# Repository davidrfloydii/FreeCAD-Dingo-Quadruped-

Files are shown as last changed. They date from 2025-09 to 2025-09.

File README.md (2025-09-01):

# FreeCAD-Dingo-Quadruped-
A repository containing the FreeCAD CAD files for the robot, firmware for microcontrollers, and code for the robot

This is a version of the original design located [here](https://github.com/Yerbert/DingoQuadruped) and is intended to recreate the core functionality utilzing all open source tools.

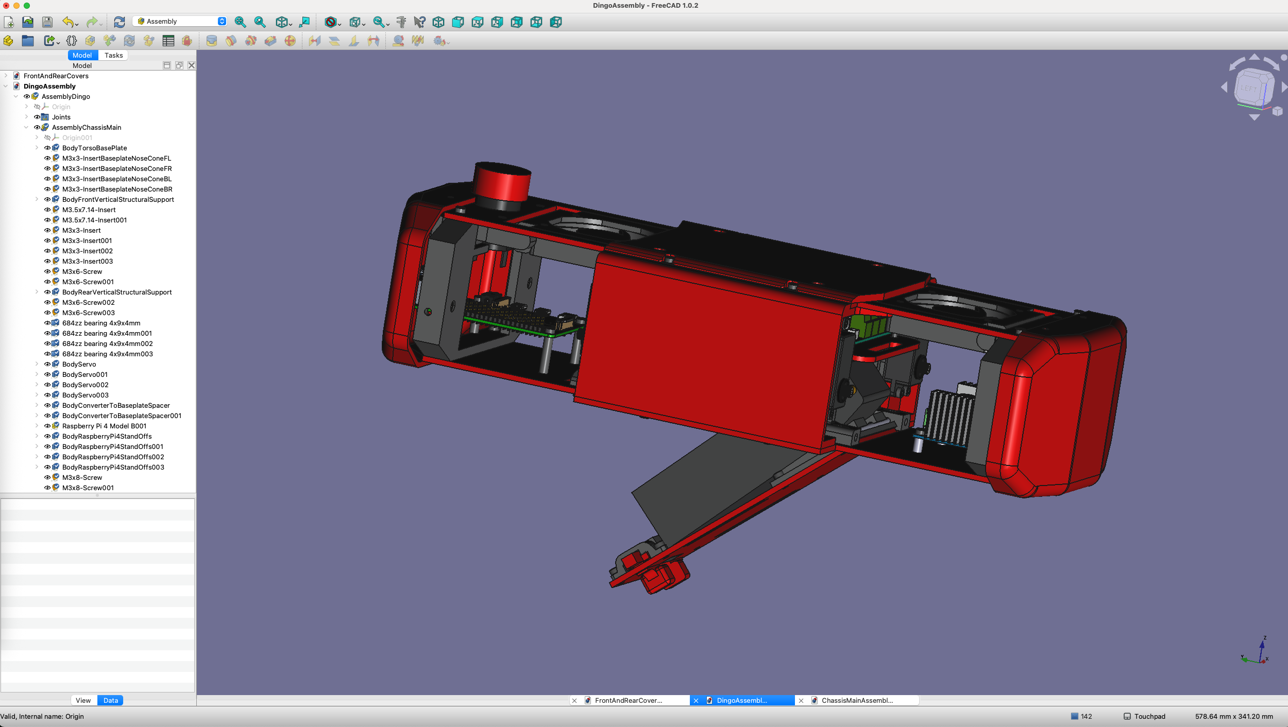
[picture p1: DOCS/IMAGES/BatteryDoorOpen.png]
Current Assembly State


# Directory Structure
The following describes the diretory structure. Note: The FreeCAD 1.0 Assembly workbench is used for putting all parts and sub-assemblies together into a single document.

-  BOM - Will hold a generated bill of materials once the assembly is completed.
-  DingoAssembly.FCStd the parent assembly to open containing the fully assembled robot.
-  EDA - Will contain KiCAD files for PCBs
-  LegParts - Contains all the CAD files that make up the legs of the robot.
-  OffTheShelfComponents - Contains standar parts that are ordered but used to positiong items in the custom parts. Some are step file format and others were modeled using FreeCAD.
-  Stand - Will contain the stand used for testing the robot.
-  SubAssemblies - Contains various SubAssemblies that are part of the parent assembly.
  -  BatteryTray - The SubAssembly for the battery holder and related parts.
  -  BL_Leg - The SubAssembly for the back left leg.
  -  BR_Leg - The SubAssembly for the back right leg.
  -  Chassis_Main - The SubAssembly that contains all of the parts of the main chassis of the robot.
  -  Fasteners - Contains standard screws, nuts, bolts, and heat inserts used from the fasteners workbench.
  -  FL_Leg - The SubAssembly for the front left leg.
  -  FR_Leg - The SubAssembly for the front right leg.
  -  Middle_Platform - The SubAssembly that sits in the center of the robot and houses various electronics components.

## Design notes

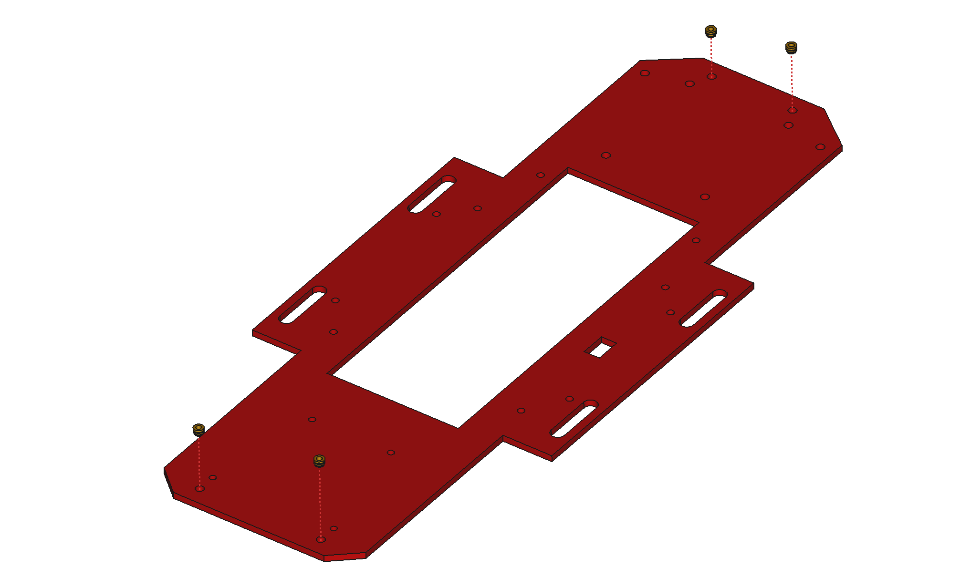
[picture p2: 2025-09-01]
SubAssemblies/Chassis_Main/Docs/Images/BaseplateHeatInserts.png

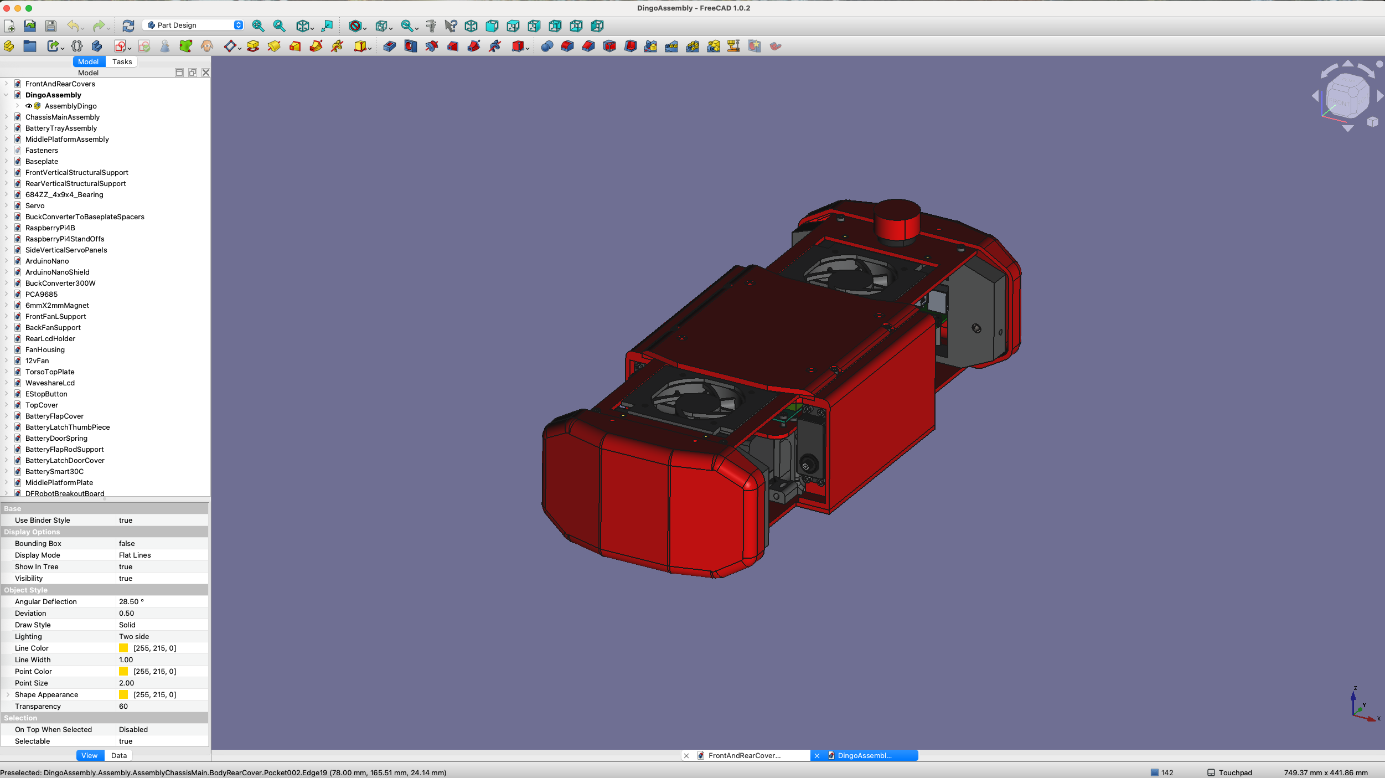
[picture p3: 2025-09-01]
DOCS/IMAGES/DingoFreeCADProject.png

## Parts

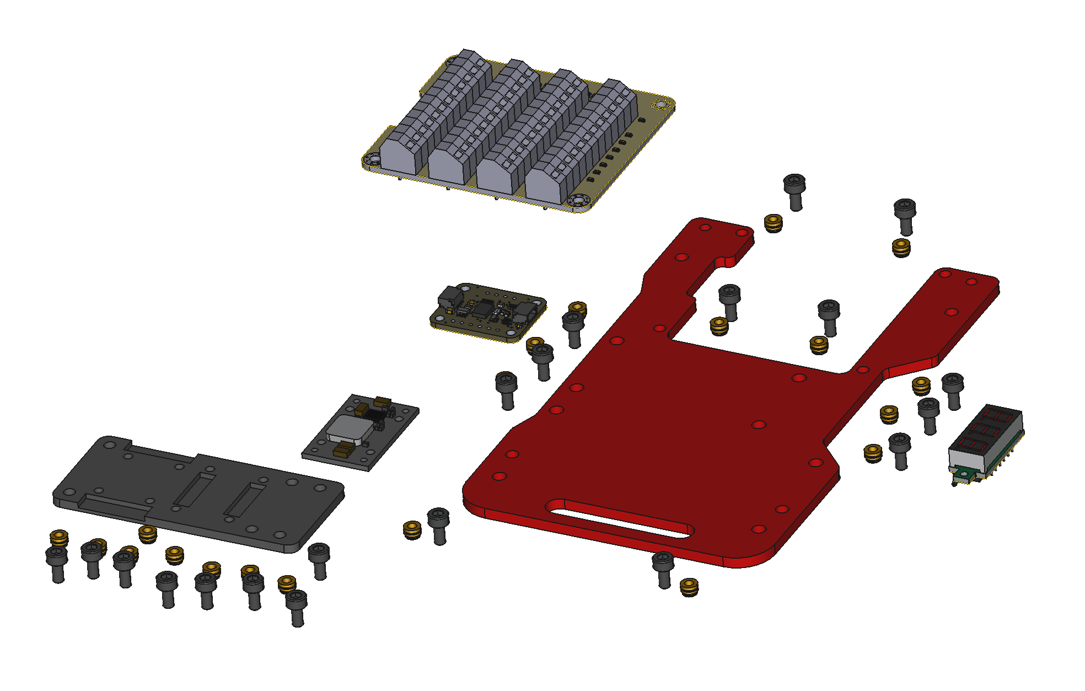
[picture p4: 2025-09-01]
SubAssemblies/Middle_Platform/Docs/Images/Middle SubAssembly Parts Laid Out.png

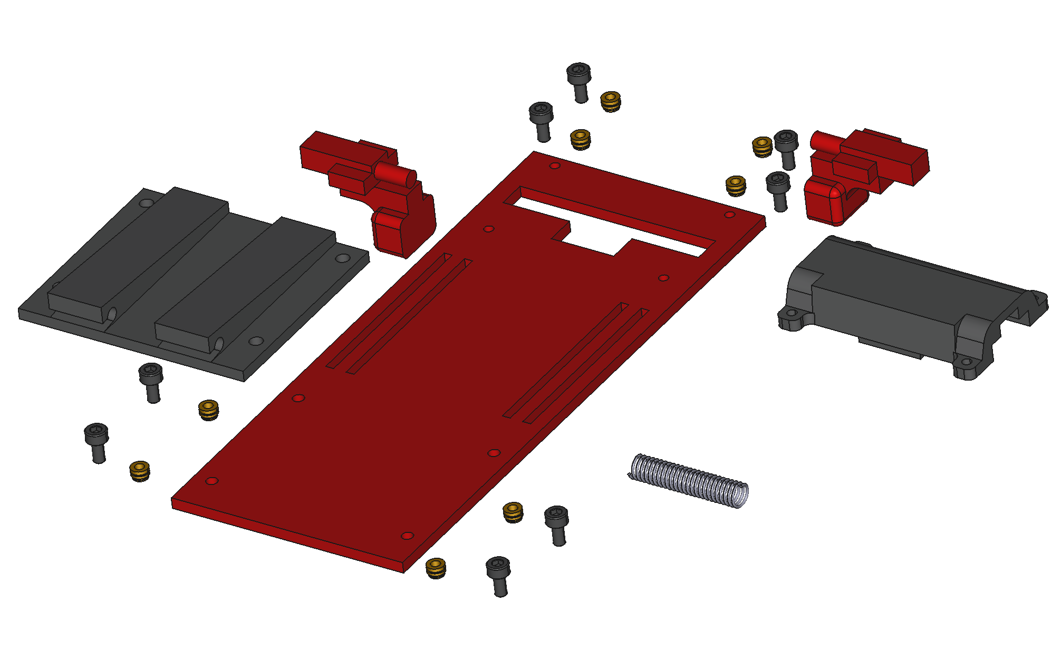
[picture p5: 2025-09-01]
SubAssemblies/BatteryTray/Docs/Images/Battery Tray SubAssembly Parts Overview.png

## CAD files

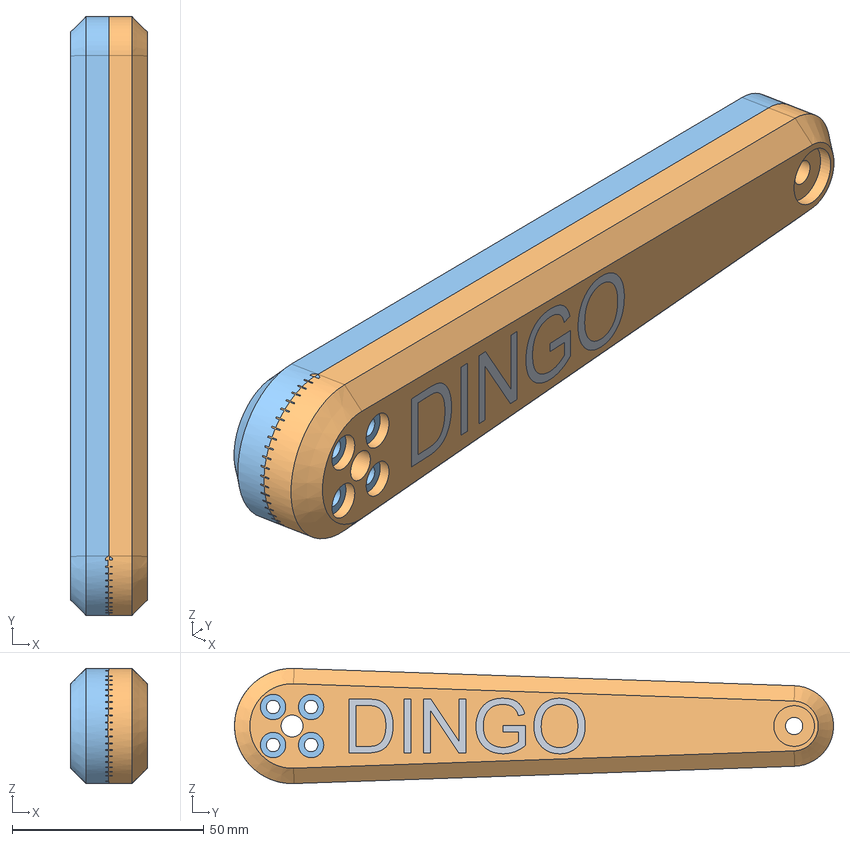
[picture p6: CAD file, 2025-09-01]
LegParts/LegUpper.FCStd
20.0 x 156.0 x 30.0 mm
BodyLegUpperCommon
BodyLegUpperRight
BodyLegUpperLeft

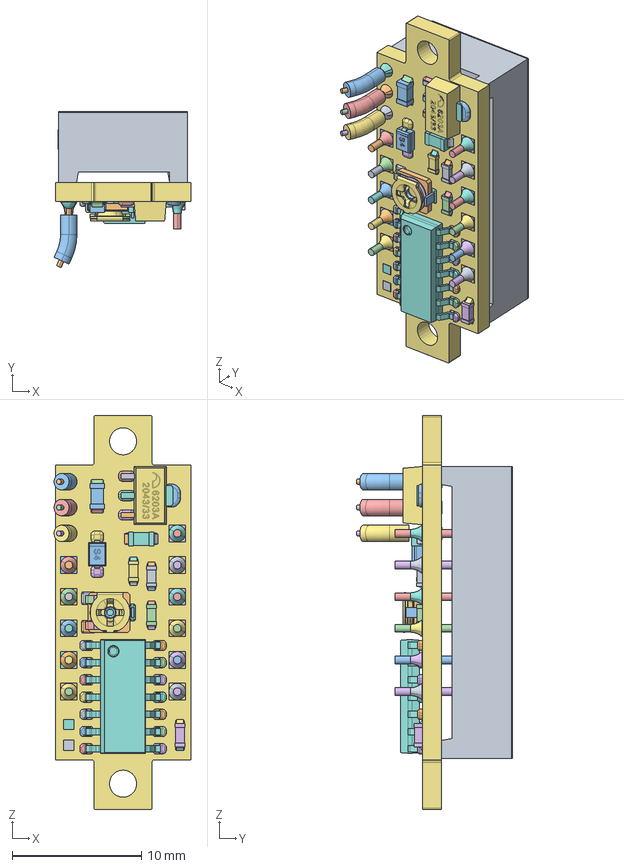
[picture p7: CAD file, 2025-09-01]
OffTheShelfComponents/BatteryLcdDisplay.FCStd
10.6 x 12.1 x 30.5 mm
Voltmeter_2,8_Display-3-Digi_DC 0V-100V_Red.stp
Voltmeter_2,8_Display-3-Digi_DC 0V-100V_Red.stp001
Voltmeter_2,8_Display-3-Digi_DC 0V-100V_Red.stp002
Voltmeter_2,8_Display-3-Digi_DC 0V-100V_Red.stp003
Voltmeter_2,8_Display-3-Digi_DC 0V-100V_Red.stp004
Voltmeter_2,8_Display-3-Digi_DC 0V-100V_Red.stp005
Voltmeter_2,8_Display-3-Digi_DC 0V-100V_Red.stp006
Voltmeter_2,8_Display-3-Digi_DC 0V-100V_Red.stp007
Voltmeter_2,8_Display-3-Digi_DC 0V-100V_Red.stp008
Voltmeter_2,8_Display-3-Digi_DC 0V-100V_Red.stp009
Voltmeter_2,8_Display-3-Digi_DC 0V-100V_Red.stp010
Voltmeter_2,8_Display-3-Digi_DC 0V-100V_Red.stp011
Voltmeter_2,8_Display-3-Digi_DC 0V-100V_Red.stp012
Voltmeter_2,8_Display-3-Digi_DC 0V-100V_Red.stp013
Voltmeter_2,8_Display-3-Digi_DC 0V-100V_Red.stp014
Voltmeter_2,8_Display-3-Digi_DC 0V-100V_Red.stp015
Voltmeter_2,8_Display-3-Digi_DC 0V-100V_Red.stp016
Voltmeter_2,8_Display-3-Digi_DC 0V-100V_Red.stp017
Voltmeter_2,8_Display-3-Digi_DC 0V-100V_Red.stp018
Voltmeter_2,8_Display-3-Digi_DC 0V-100V_Red.stp019
Voltmeter_2,8_Display-3-Digi_DC 0V-100V_Red.stp020
Voltmeter_2,8_Display-3-Digi_DC 0V-100V_Red.stp021
Voltmeter_2,8_Display-3-Digi_DC 0V-100V_Red.stp022
Voltmeter_2,8_Display-3-Digi_DC 0V-100V_Red.stp023
Voltmeter_2,8_Display-3-Digi_DC 0V-100V_Red.stp024
Voltmeter_2,8_Display-3-Digi_DC 0V-100V_Red.stp025
Voltmeter_2,8_Display-3-Digi_DC 0V-100V_Red.stp026
Voltmeter_2,8_Display-3-Digi_DC 0V-100V_Red.stp027
Voltmeter_2,8_Display-3-Digi_DC 0V-100V_Red.stp028
Voltmeter_2,8_Display-3-Digi_DC 0V-100V_Red.stp029
Voltmeter_2,8_Display-3-Digi_DC 0V-100V_Red.stp030
Voltmeter_2,8_Display-3-Digi_DC 0V-100V_Red.stp031
Voltmeter_2,8_Display-3-Digi_DC 0V-100V_Red.stp032
Voltmeter_2,8_Display-3-Digi_DC 0V-100V_Red.stp033
Voltmeter_2,8_Display-3-Digi_DC 0V-100V_Red.stp034
Voltmeter_2,8_Display-3-Digi_DC 0V-100V_Red.stp035
Voltmeter_2,8_Display-3-Digi_DC 0V-100V_Red.stp036
Voltmeter_2,8_Display-3-Digi_DC 0V-100V_Red.stp037
Voltmeter_2,8_Display-3-Digi_DC 0V-100V_Red.stp038
Voltmeter_2,8_Display-3-Digi_DC 0V-100V_Red.stp039
Voltmeter_2,8_Display-3-Digi_DC 0V-100V_Red.stp040
Voltmeter_2,8_Display-3-Digi_DC 0V-100V_Red.stp041
Voltmeter_2,8_Display-3-Digi_DC 0V-100V_Red.stp042
Voltmeter_2,8_Display-3-Digi_DC 0V-100V_Red.stp043
Voltmeter_2,8_Display-3-Digi_DC 0V-100V_Red.stp044
Voltmeter_2,8_Display-3-Digi_DC 0V-100V_Red.stp045
Voltmeter_2,8_Display-3-Digi_DC 0V-100V_Red.stp046
Voltmeter_2,8_Display-3-Digi_DC 0V-100V_Red.stp047
Voltmeter_2,8_Display-3-Digi_DC 0V-100V_Red.stp048
Voltmeter_2,8_Display-3-Digi_DC 0V-100V_Red.stp049
Voltmeter_2,8_Display-3-Digi_DC 0V-100V_Red.stp050
Voltmeter_2,8_Display-3-Digi_DC 0V-100V_Red.stp051
Voltmeter_2,8_Display-3-Digi_DC 0V-100V_Red.stp052
Voltmeter_2,8_Display-3-Digi_DC 0V-100V_Red.stp053
Voltmeter_2,8_Display-3-Digi_DC 0V-100V_Red.stp054
Voltmeter_2,8_Display-3-Digi_DC 0V-100V_Red.stp055
Voltmeter_2,8_Display-3-Digi_DC 0V-100V_Red.stp056
Voltmeter_2,8_Display-3-Digi_DC 0V-100V_Red.stp057
Voltmeter_2,8_Display-3-Digi_DC 0V-100V_Red.stp058
Voltmeter_2,8_Display-3-Digi_DC 0V-100V_Red.stp059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

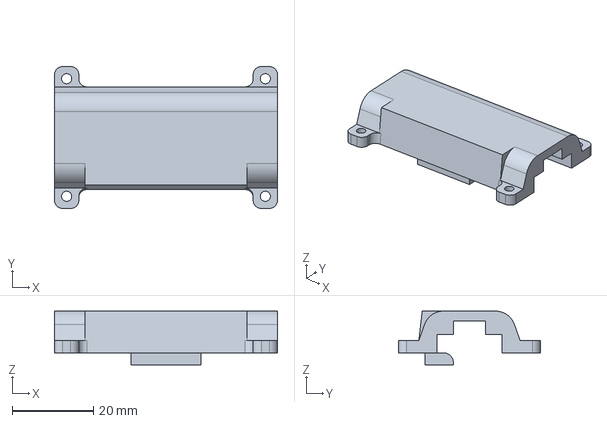
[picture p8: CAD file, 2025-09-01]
SubAssemblies/BatteryTray/Parts/BatteryLatchDoorCover.FCStd
55.0 x 35.0 x 13.3 mm

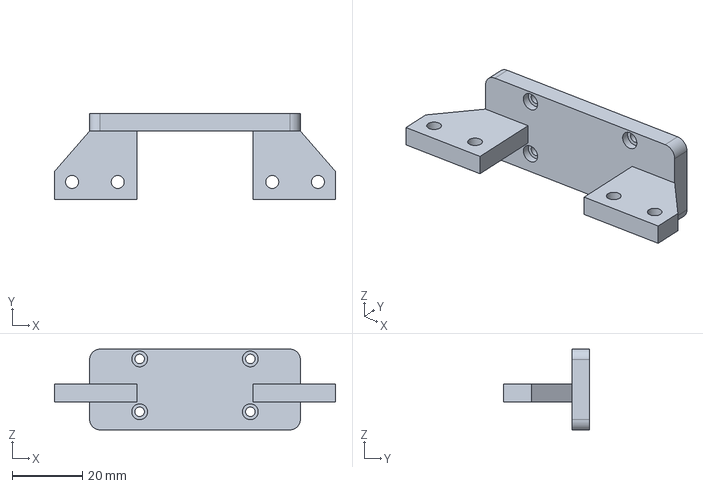
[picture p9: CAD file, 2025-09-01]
SubAssemblies/Chassis_Main/Parts/RearLcdHolder.FCStd
80.0 x 24.5 x 23.0 mm

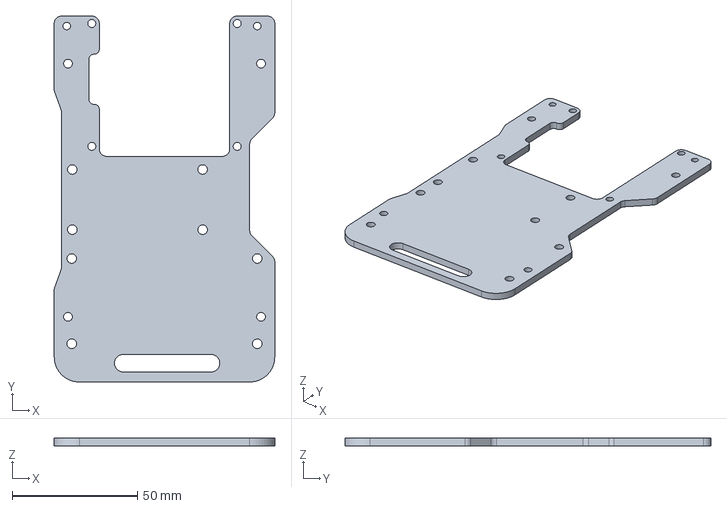
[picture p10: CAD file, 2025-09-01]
SubAssemblies/Middle_Platform/Parts/MiddlePlatformPlate.FCStd
88.0 x 146.0 x 3.00 mm

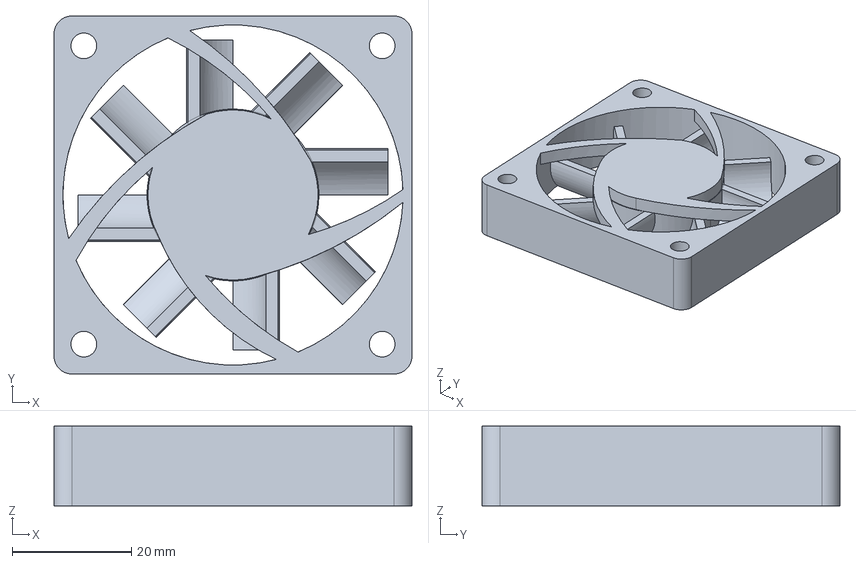
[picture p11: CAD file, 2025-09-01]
OffTheShelfComponents/12vFan.FCStd
60.0 x 60.0 x 13.4 mm

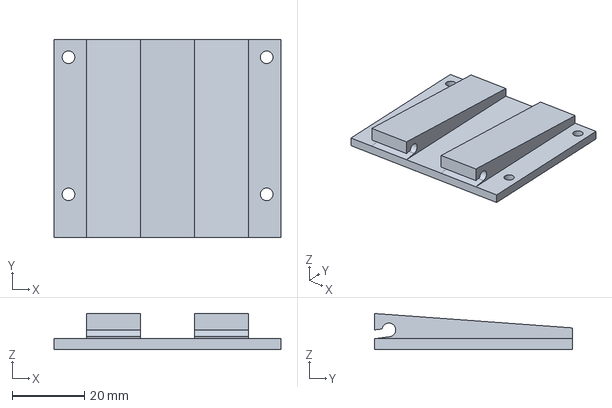
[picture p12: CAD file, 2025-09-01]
SubAssemblies/BatteryTray/Parts/BatteryFlapRodSupport.FCStd
63.0 x 55.0 x 10.0 mm

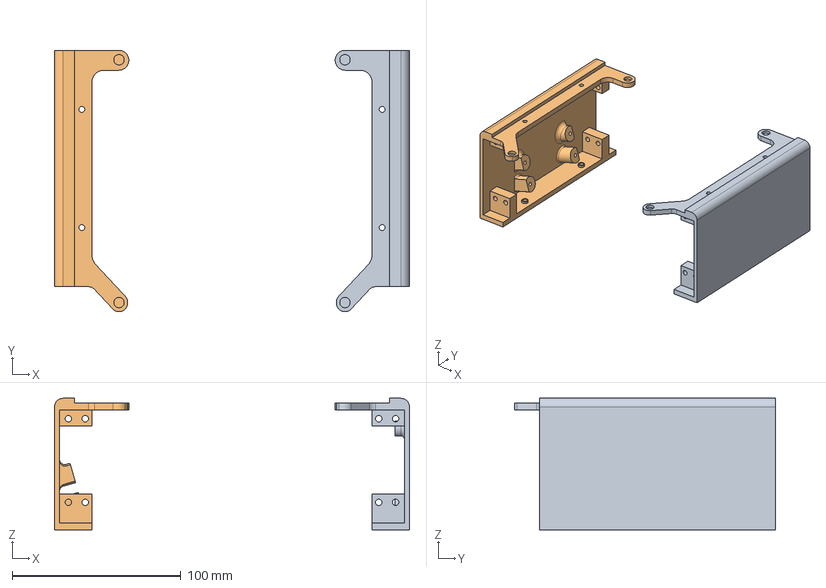
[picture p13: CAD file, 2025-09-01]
SubAssemblies/Chassis_Main/Parts/SideVerticalServoPanels.FCStd
210.2 x 154.8 x 77.9 mm
BodyRightSideVerticalServoPanel
BodyLeftSideVerticalServoPanel

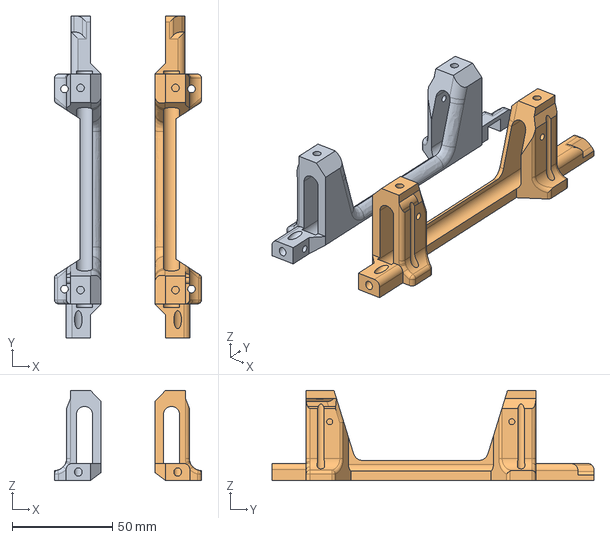
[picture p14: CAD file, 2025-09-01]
SubAssemblies/Middle_Platform/Parts/LeftInnerVerticalSupport.FCStd
73.4 x 160.8 x 45.0 mm
BodyLeftInnerVerticalSupport
BodyRightInnerVerticalSupport

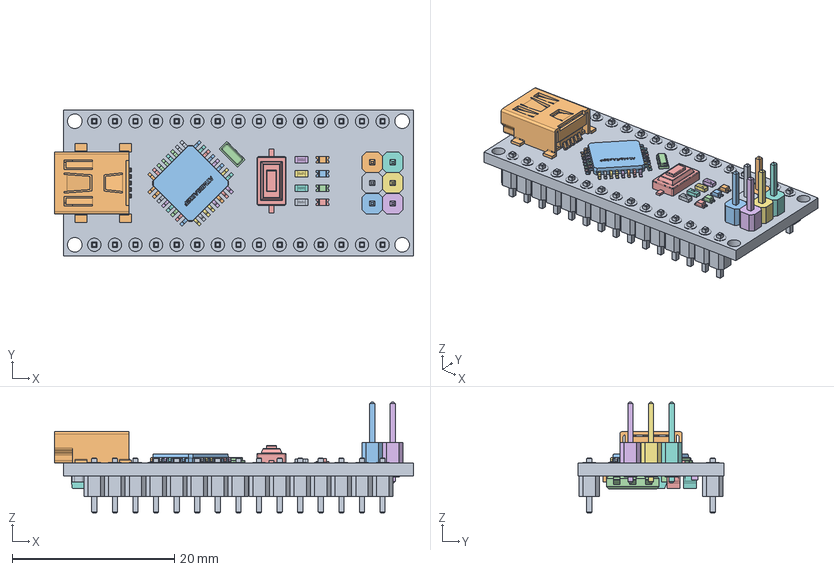
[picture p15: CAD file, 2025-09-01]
OffTheShelfComponents/ArduinoNano.FCStd
44.3 x 18.0 x 13.7 mm
Arduino Nano
Mini USB
ATMEGA328P-AU--3DModel-STEP-56544.step.STEP.STEP.STEP
ATMEGA328P-AU--3DModel-STEP-56544.step.STEP.STEP.STEP001
ATMEGA328P-AU--3DModel-STEP-56544.step.STEP.STEP.STEP002
ATMEGA328P-AU--3DModel-STEP-56544.step.STEP.STEP.STEP003
ATMEGA328P-AU--3DModel-STEP-56544.step.STEP.STEP.STEP004
ATMEGA328P-AU--3DModel-STEP-56544.step.STEP.STEP.STEP005
ATMEGA328P-AU--3DModel-STEP-56544.step.STEP.STEP.STEP006
ATMEGA328P-AU--3DModel-STEP-56544.step.STEP.STEP.STEP007
ATMEGA328P-AU--3DModel-STEP-56544.step.STEP.STEP.STEP008
ATMEGA328P-AU--3DModel-STEP-56544.step.STEP.STEP.STEP009
ATMEGA328P-AU--3DModel-STEP-56544.step.STEP.STEP.STEP010
ATMEGA328P-AU--3DModel-STEP-56544.step.STEP.STEP.STEP011
ATMEGA328P-AU--3DModel-STEP-56544.step.STEP.STEP.STEP012
ATMEGA328P-AU--3DModel-STEP-56544.step.STEP.STEP.STEP013
ATMEGA328P-AU--3DModel-STEP-56544.step.STEP.STEP.STEP014
ATMEGA328P-AU--3DModel-STEP-56544.step.STEP.STEP.STEP015
ATMEGA328P-AU--3DModel-STEP-56544.step.STEP.STEP.STEP016
ATMEGA328P-AU--3DModel-STEP-56544.step.STEP.STEP.STEP017
ATMEGA328P-AU--3DModel-STEP-56544.step.STEP.STEP.STEP018
ATMEGA328P-AU--3DModel-STEP-56544.step.STEP.STEP.STEP019
ATMEGA328P-AU--3DModel-STEP-56544.step.STEP.STEP.STEP020
ATMEGA328P-AU--3DModel-STEP-56544.step.STEP.STEP.STEP021
ATMEGA328P-AU--3DModel-STEP-56544.step.STEP.STEP.STEP022
ATMEGA328P-AU--3DModel-STEP-56544.step.STEP.STEP.STEP023
ATMEGA328P-AU--3DModel-STEP-56544.step.STEP.STEP.STEP024
ATMEGA328P-AU--3DModel-STEP-56544.step.STEP.STEP.STEP025
ATMEGA328P-AU--3DModel-STEP-56544.step.STEP.STEP.STEP026
ATMEGA328P-AU--3DModel-STEP-56544.step.STEP.STEP.STEP027
ATMEGA328P-AU--3DModel-STEP-56544.step.STEP.STEP.STEP028
ATMEGA328P-AU--3DModel-STEP-56544.step.STEP.STEP.STEP029
ATMEGA328P-AU--3DModel-STEP-56544.step.STEP.STEP.STEP030
ATMEGA328P-AU--3DModel-STEP-56544.step.STEP.STEP.STEP031
ATMEGA328P-AU--3DModel-STEP-56544.step.STEP.STEP.STEP032
CSTCE Crystal
2Pin Tactile Switch 6x3.6
0603 Resistor
0603 Resistor001
0603 Resistor002
0603 Resistor003
Blue LED
Green LED
Red LED
Blue LED001
Header 2x3
Header 2x004
Header 2x005
Header 2x006
Header 2x007
Header 2x008
SOT89
1206 Tantalum
0603 Resistor004
0603 Capacitor
1206 Tantalum001
0603 Capacitor001
0603 Capacitor002
0603 Capacitor003
0603 Capacitor004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

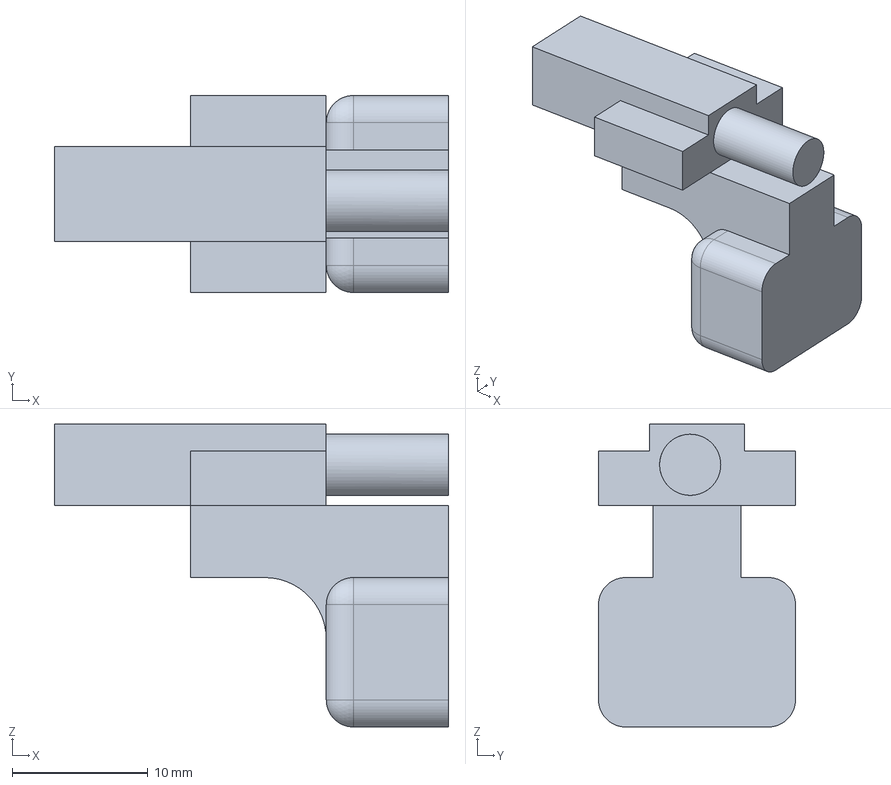
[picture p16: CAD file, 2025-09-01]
SubAssemblies/BatteryTray/Parts/BatteryLatchThumbPiece.FCStd
29.0 x 14.5 x 22.3 mm

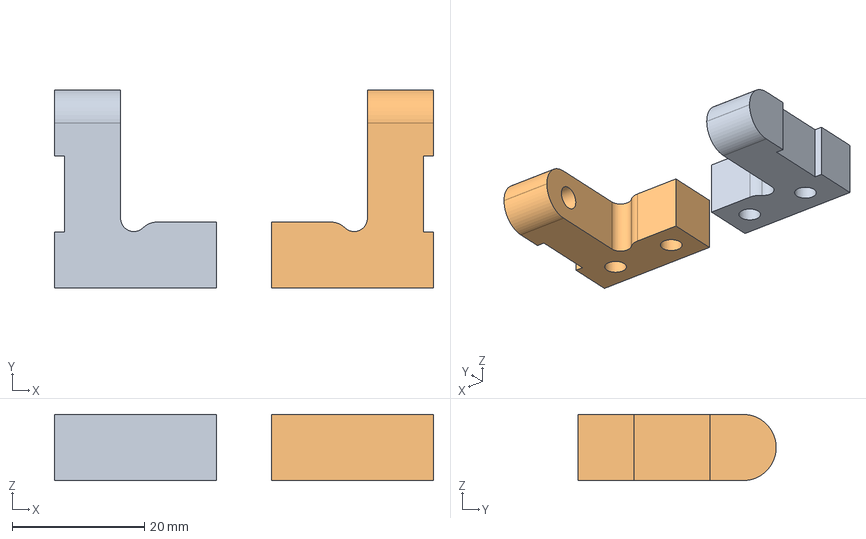
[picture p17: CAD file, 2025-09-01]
SubAssemblies/Chassis_Main/Parts/FrontFanLSupport.FCStd
57.3 x 30.0 x 10.0 mm
BodyFrontFanSupportLeft
BodyFrontFanSupportRight

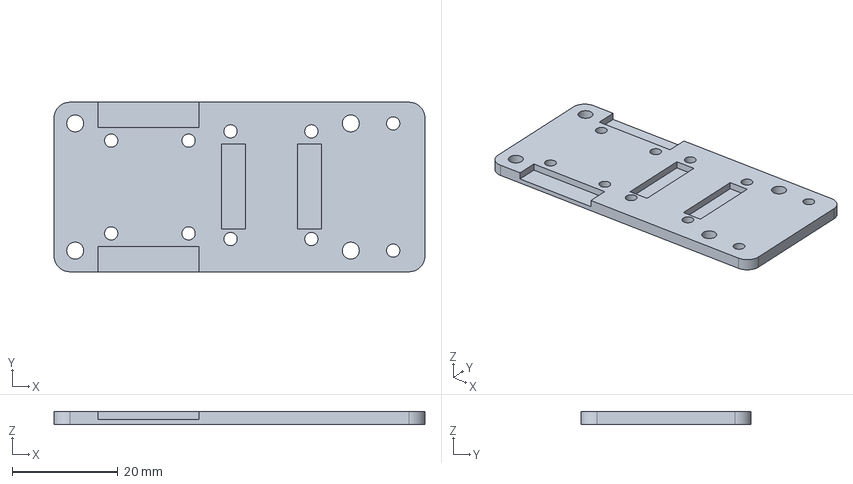
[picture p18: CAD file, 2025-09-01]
SubAssemblies/Middle_Platform/Parts/ImuAndBuckHolder.FCStd
70.0 x 32.0 x 2.50 mm

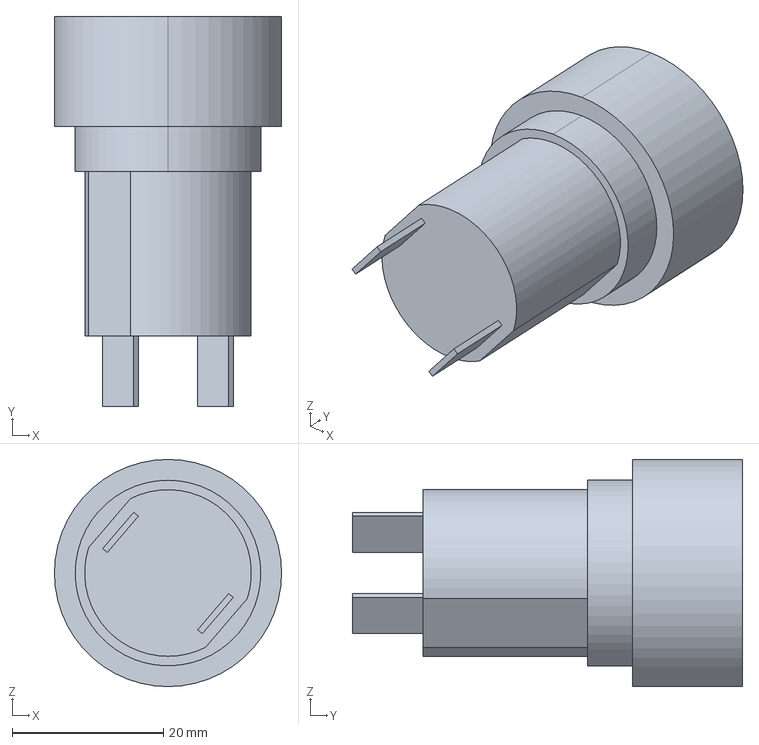
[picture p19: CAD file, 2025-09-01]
OffTheShelfComponents/EStopButton.FCStd
30.0 x 51.5 x 30.0 mm

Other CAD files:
DingoAssembly.FCStd
SubAssemblies/BatteryTray/BatteryTrayAssembly.FCStd
SubAssemblies/Chassis_Main/ChassisMainAssembly.FCStd
SubAssemblies/Middle_Platform/MiddlePlatformAssembly.FCStd
OffTheShelfComponents/5VBuckConverter.FCStd
OffTheShelfComponents/684ZZ_4x9x4_Bearing.FCStd
OffTheShelfComponents/6mmX2mmMagnet.FCStd
OffTheShelfComponents/BatterySmart30C.FCStd
OffTheShelfComponents/BuckConverter300W.FCStd
OffTheShelfComponents/Imu.FCStd
OffTheShelfComponents/PCA9685.FCStd
OffTheShelfComponents/RaspberryPi4B.FCStd
OffTheShelfComponents/Servo.FCStd
OffTheShelfComponents/WaveshareLcd.FCStd
SubAssemblies/BatteryTray/Parts/BatteryDoorHingeRod.FCStd
SubAssemblies/BatteryTray/Parts/BatteryDoorSpring.FCStd
SubAssemblies/BatteryTray/Parts/BatteryFlapCover.FCStd
SubAssemblies/Chassis_Main/Parts/BackFanSupport.FCStd
SubAssemblies/Chassis_Main/Parts/Baseplate.FCStd
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

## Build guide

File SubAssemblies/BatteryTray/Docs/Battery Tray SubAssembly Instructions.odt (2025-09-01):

# Battery Tray Sub Assembly

The following are a list of the parts needed for this sub-assembly. Items that need to be 3D printed are highlighted in the column named “3D Printed”.

Name | Qty | 3D Printed?
Battery Flap Cover | 1 | Y
Battery Door Spring | 1 | N
Battery Flap Rod Support | 1 | Y
Battery Latch Thumb Piece L | 1 | Y
Battery Latch Thumb Piece R | 1 | Y
M3x3mm Heat Insert | 8 | N
M3x6mm Hex Cap Screws | 8 | N

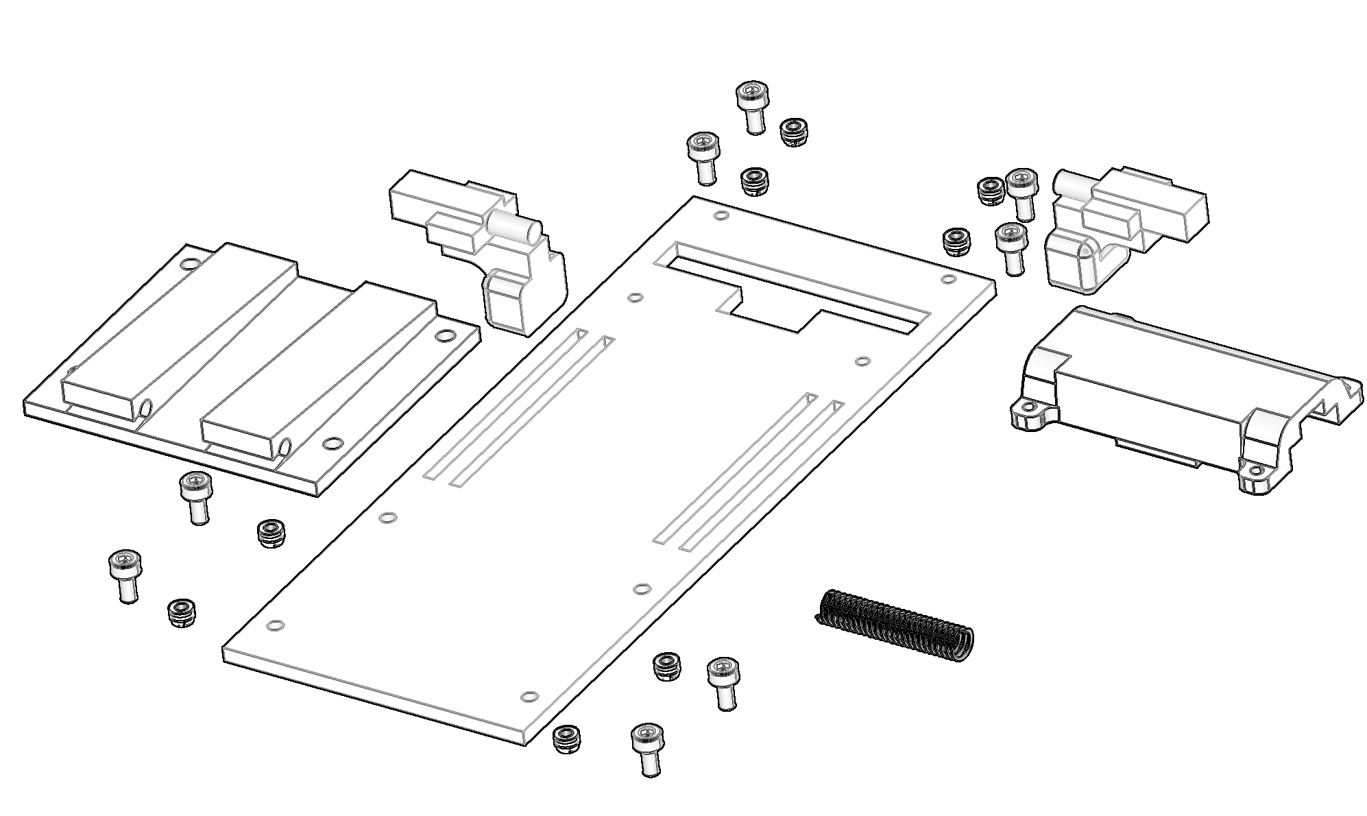
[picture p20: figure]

## Step 1.

Start by inserting all 8 of the heat inserts into the cover. These go in from the top side down.

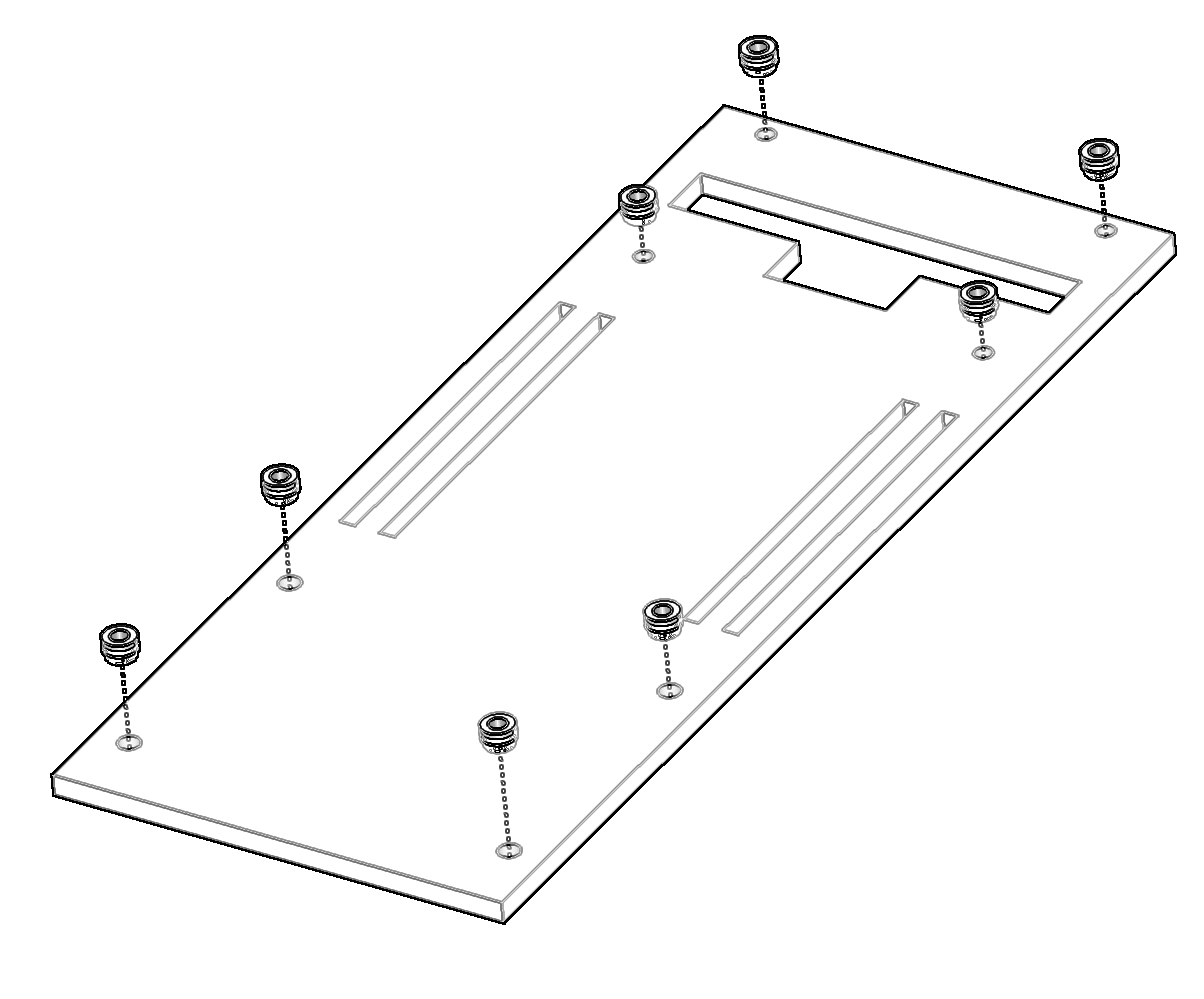
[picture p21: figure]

## Step 2.

Start by flipping the cover upside down. From the bottom side of the cover angle each thumb piece so they can fit through the larger center opening. Once in far enough, rotate and push each to the outside.

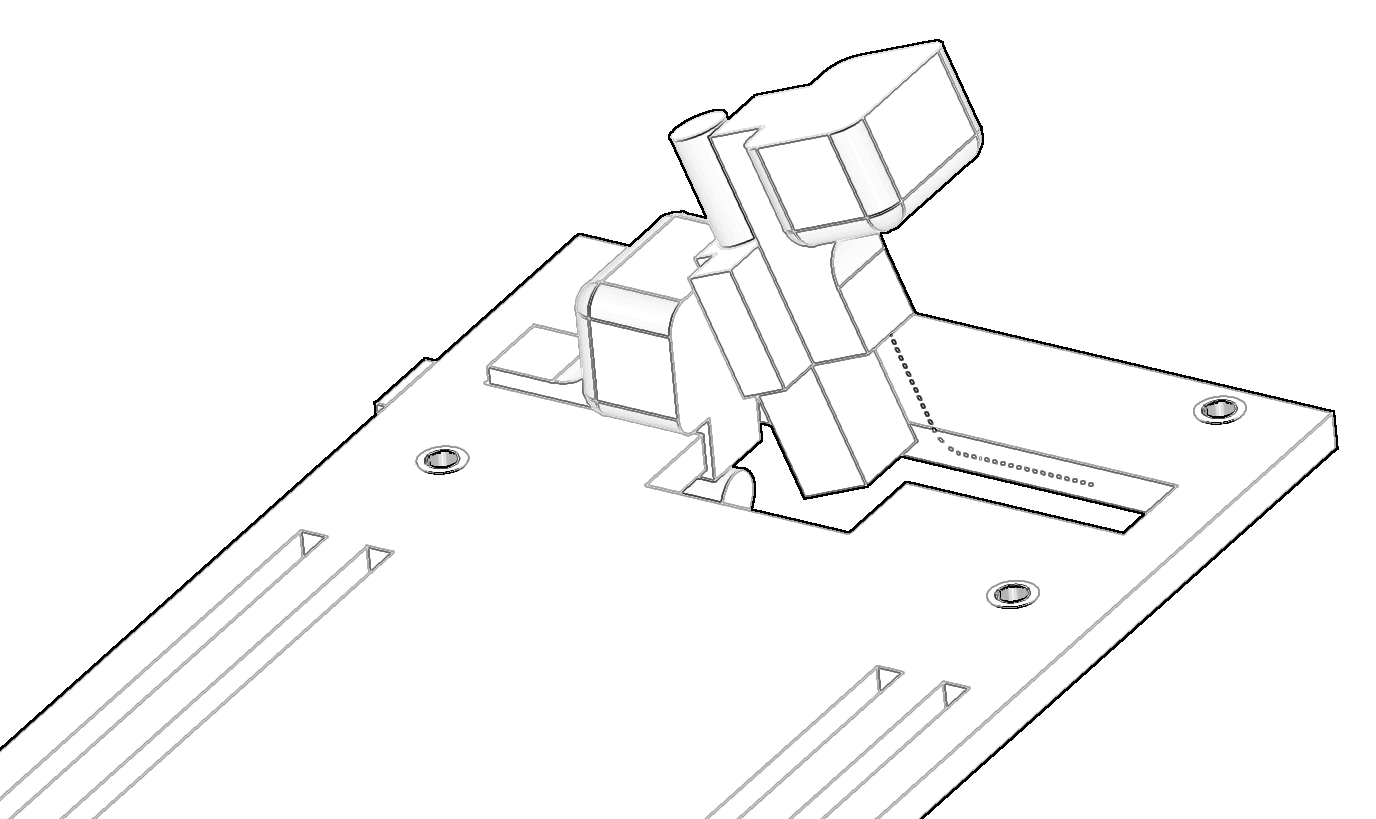
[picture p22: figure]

Then hold each thumb piece in place while rotating the cover back over to its original position. The result should look like this and prepare you for spring isertion.

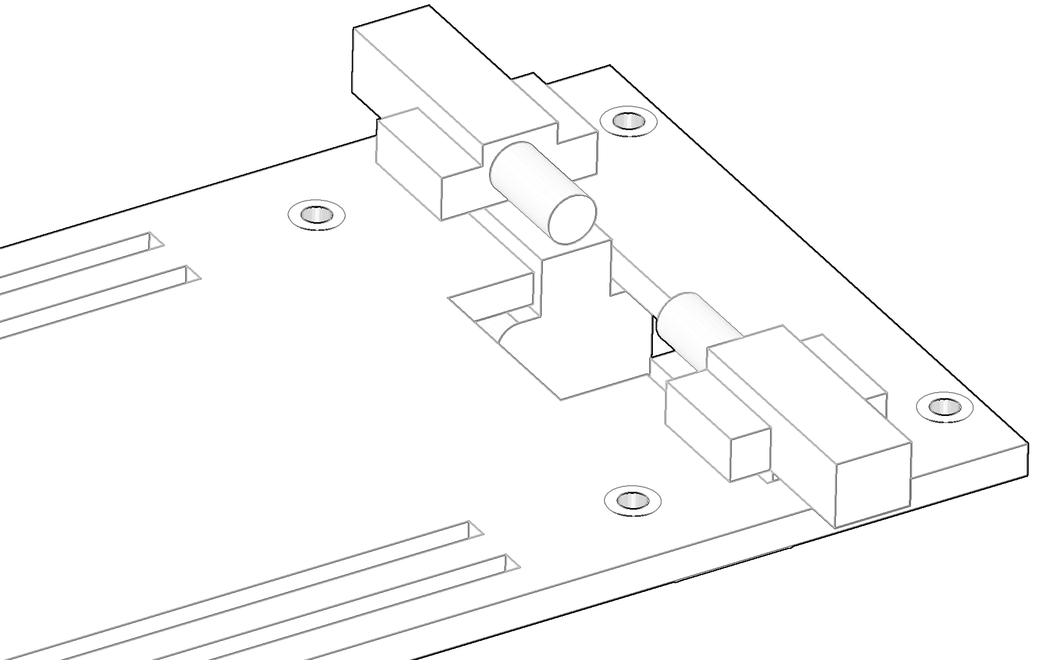
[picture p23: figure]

## Step 3.

Bend and install the spring in between the two thumb pieces. Once installed it should put strong outward pressure on both thumb pieces. This keeps them engaged with the main body so that the battery door does not open accidentally.

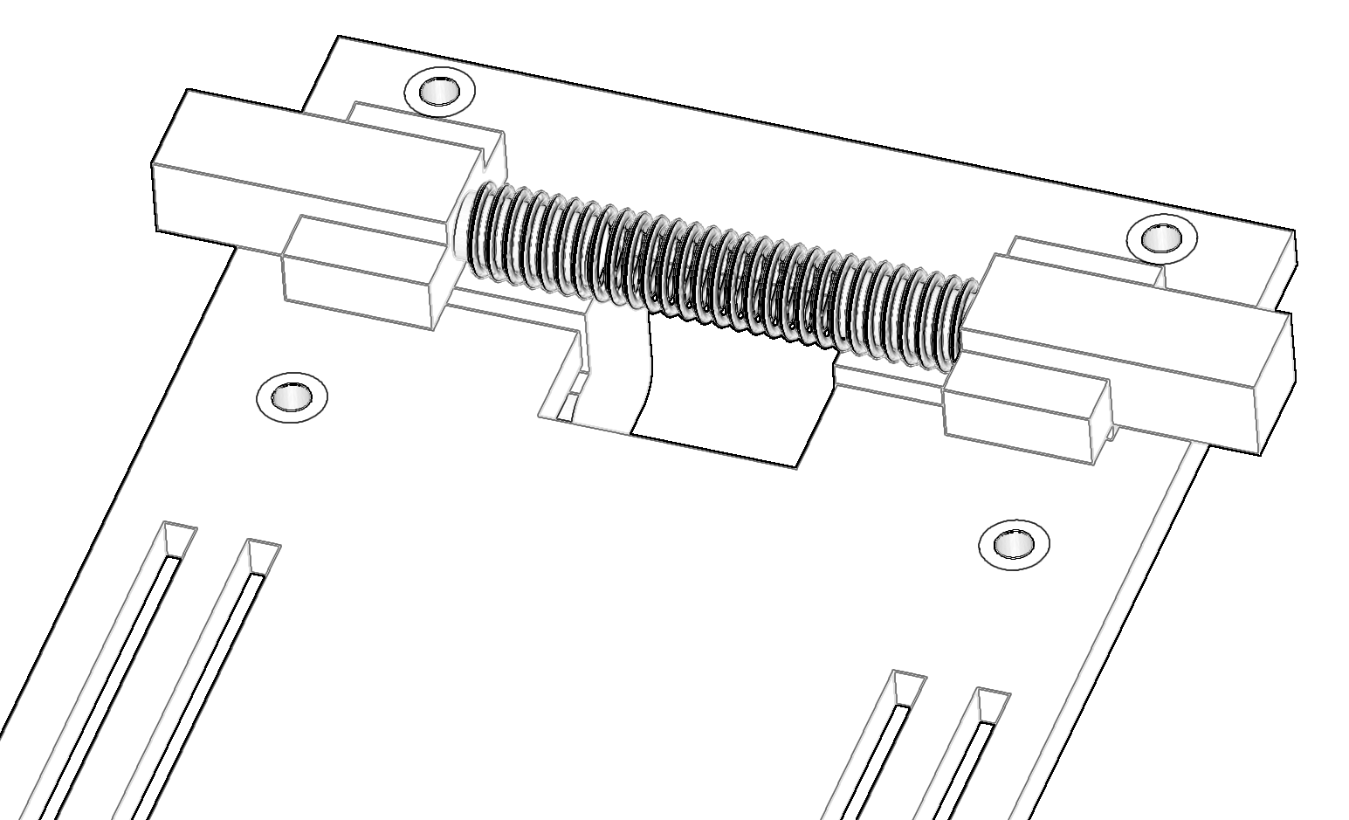
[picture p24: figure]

## Step 4.

Next, install the spring and latch cover to retain the spring in place during compression and keep items from being pinched. This is done using 4 of the M3x6mm screws threading into the heat inserts installed previously.

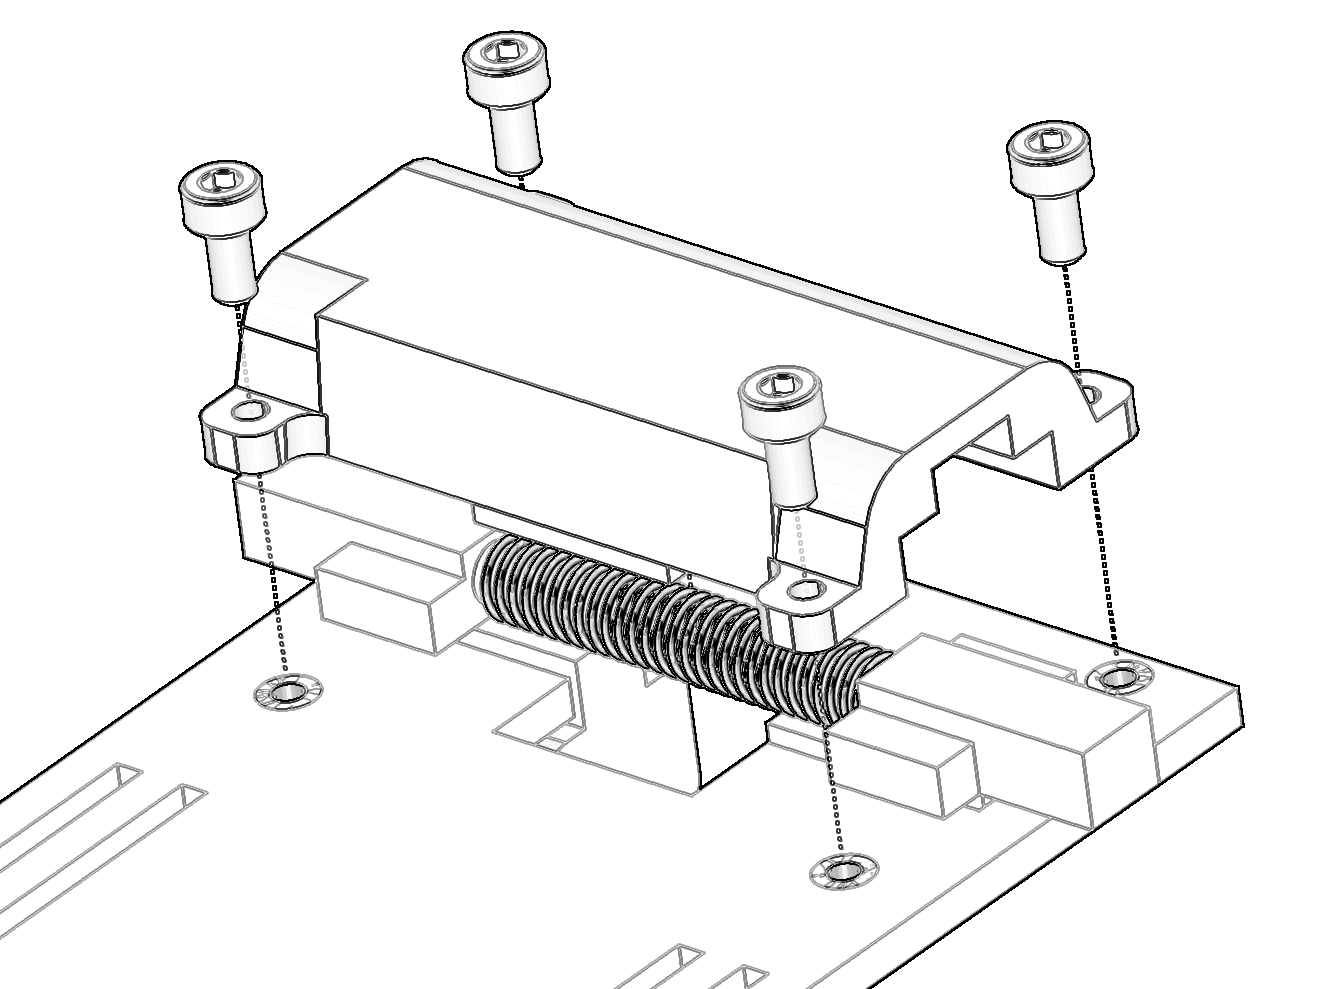
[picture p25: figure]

## Step 5.

Once completed you can install the battery support piece that provides the pivot joint for the battery door, and provides support to the battery to keep it angled upward. This is attached again utilizing 4 more of the M3x6mm screws threading into the corresponding heat inserts.

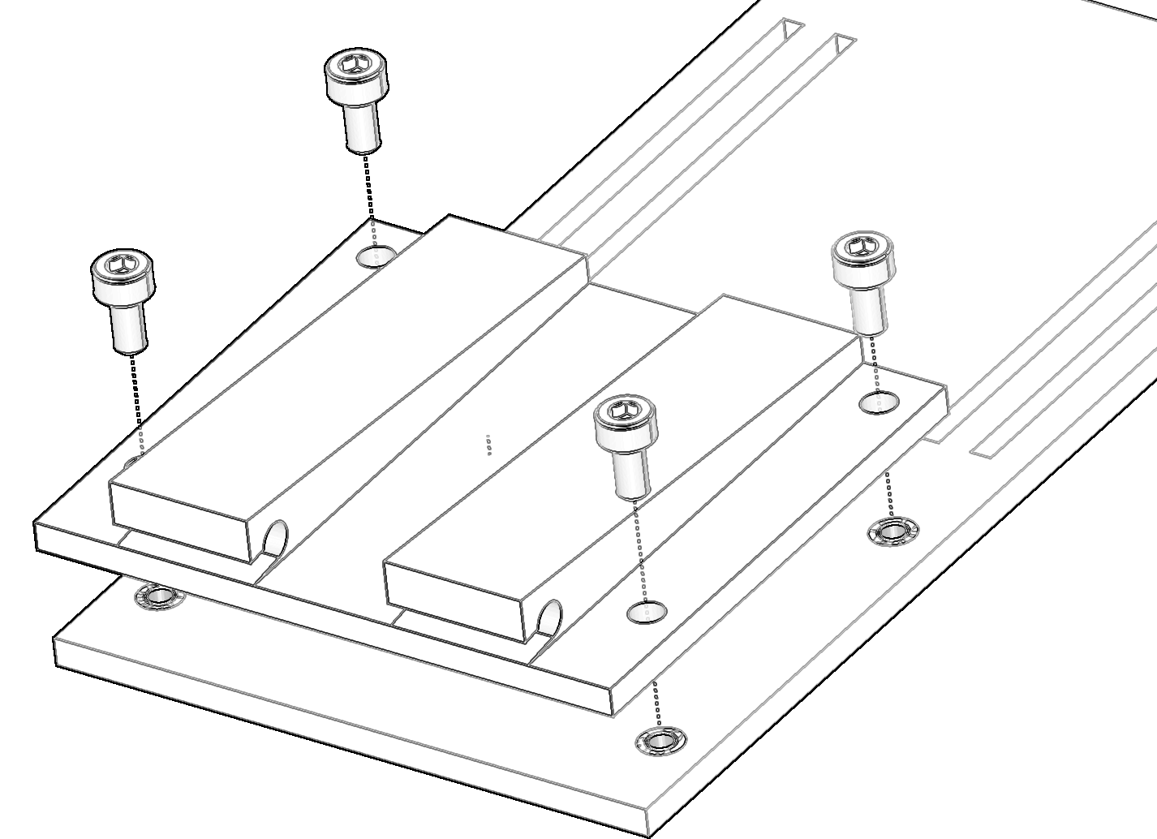
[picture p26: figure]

## Complete

Congratulations you’ve completed the assembly of the battery tray sub-assembly. Simply ensure the thumb releases compress the spring and move inwards to release the tray. They should move close to one another, but not far enough that the pieces can come out of the cover.

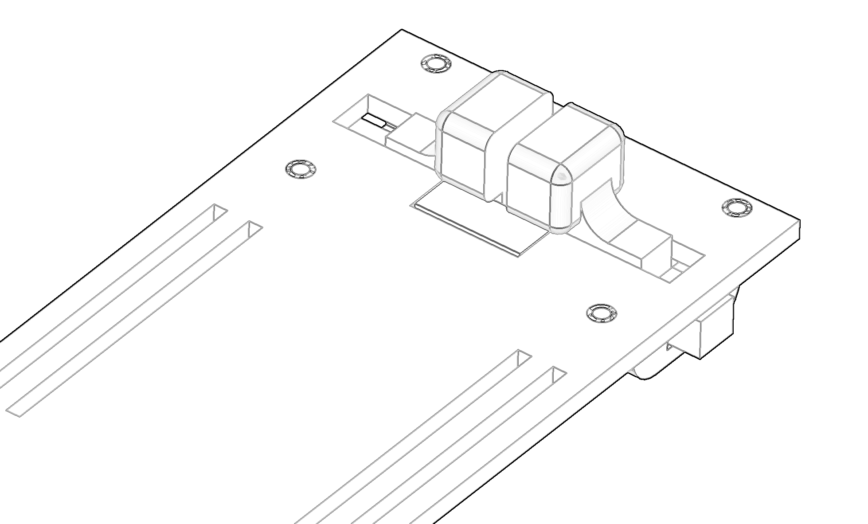
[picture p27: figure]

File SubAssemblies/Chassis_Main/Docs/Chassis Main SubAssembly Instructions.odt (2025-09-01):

# Main Chassis Sub Assembly

The following are a list of the parts needed for this sub-assembly. Items that need to be 3D printed are highlighted in the column named “3D Printed”.

Name | Qty | 3D Printed?
Body Torso Baseplate | 1 | N (Optional 2-Piece Avl.)
M3x3mm Hex Cap Screws | 4 | N
Front Vertical Structural Support | 1 | Y
Rear Vertical Structural Support | 1 | Y
M3.5x7.14mm Heat Insert | | N
M3x3mm Heat Insert | | N
M3x6mm Hex Cap Screw | | N
684ZZ 4x9x4mm Bearing | 4 | N

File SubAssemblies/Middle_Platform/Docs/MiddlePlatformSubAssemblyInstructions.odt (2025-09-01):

# Middle Plate Sub Assembly

The following are a list of parts needed for this sub-assembly. Items that need to be 3D printed are highlighted in the column named “3D Printed’.

Name | Qty | 3D Printed?
DFRobot Breakout Board | 1 | No
M3x3mm Heat Isert | 10 | No
Voltmeter LCD Disiplay | 1 | No
Adafruit BNO055 IMU | 1 | No
DFRobot 5V Buck Converter | 1 | No
IMU and Buck Holder | 1 | Yes
M3x6mm Hex Cap Screw
M2.5x3mm Heat Inserts | 10

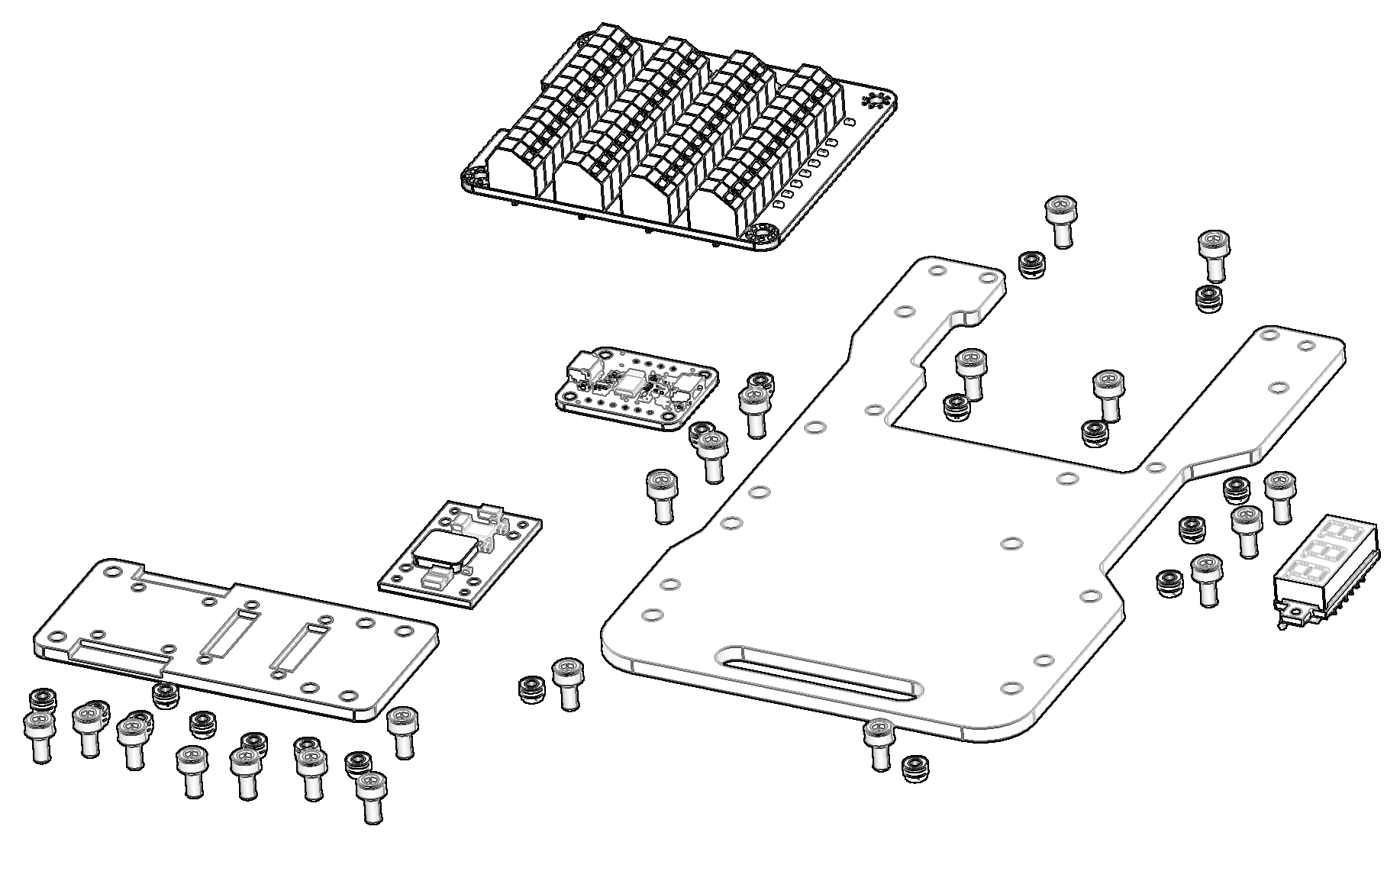
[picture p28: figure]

## Step 1.

The first step is to install the heat inserts into the appropriate locations on the IMU and Buck Holder. Note that not all holes receive an insert. Those are left open to attach the platform to the vertical pieces on the main chassis.

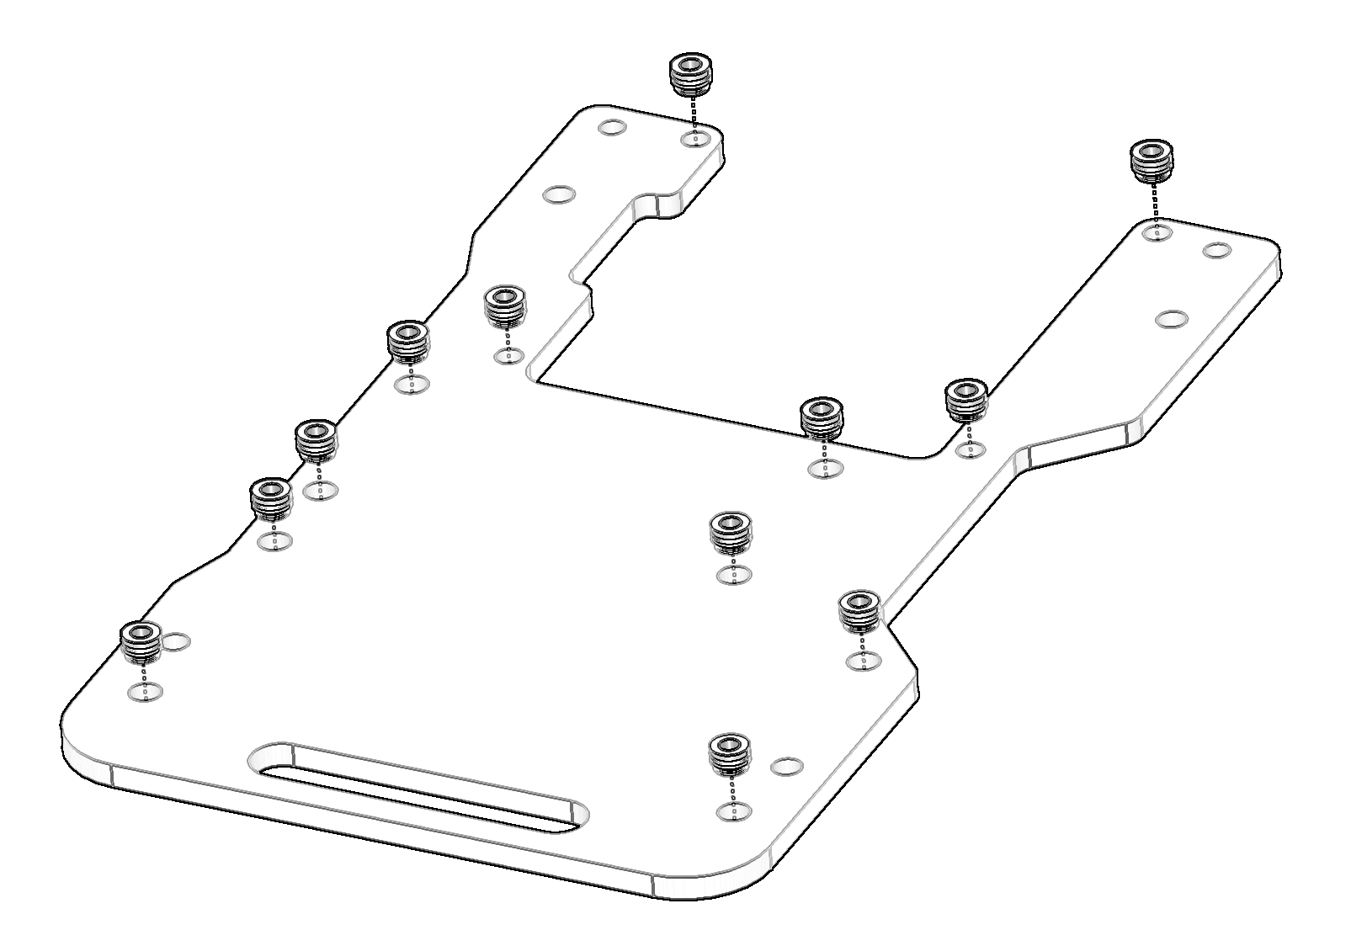
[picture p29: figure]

## Step 2.

Next, we will place the heat inserts into the appropriate holes for the IMU Holder. These are the M2.5x3mm heat inserts.

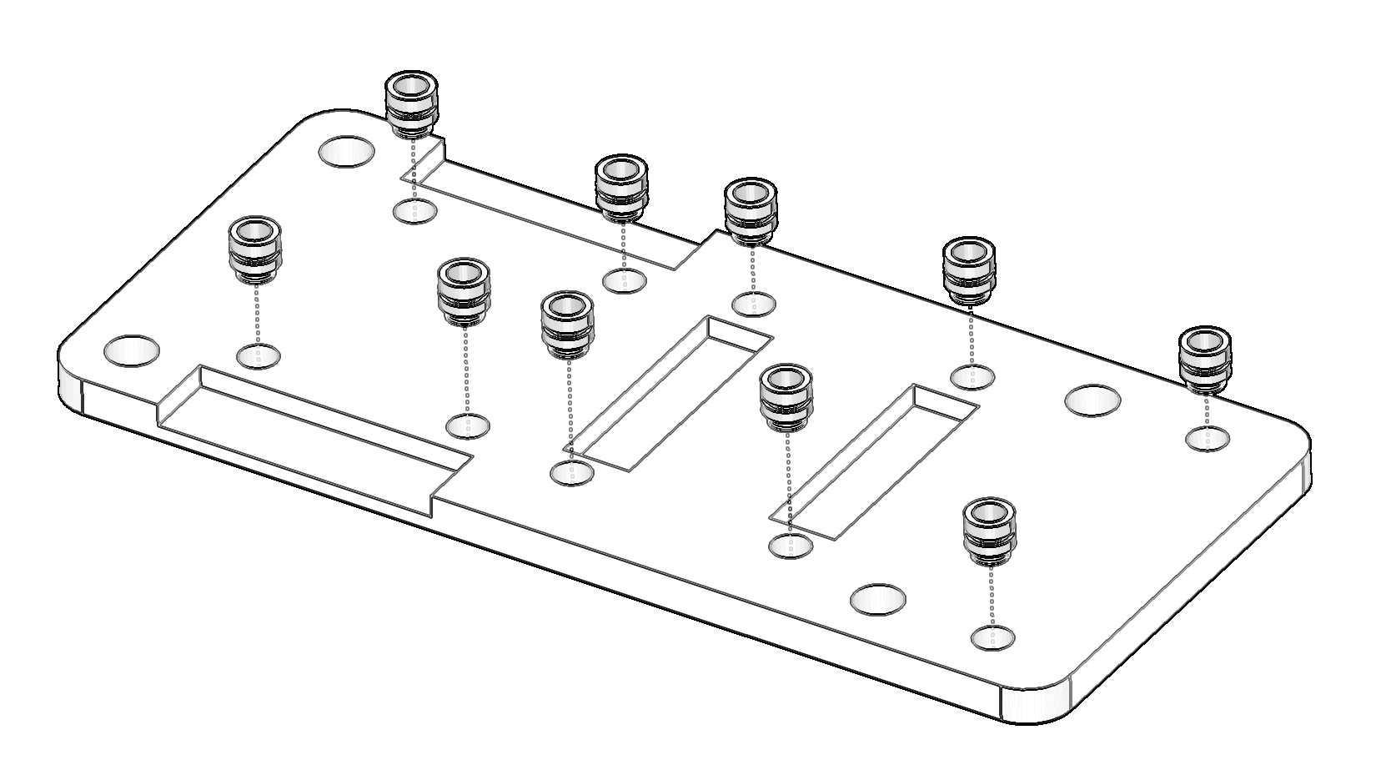
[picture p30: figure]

Step 3.

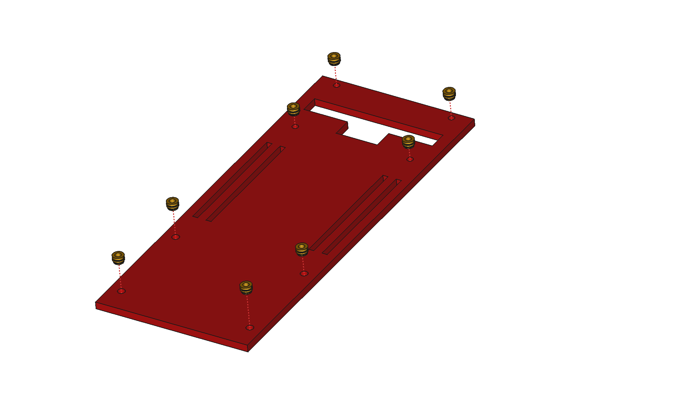
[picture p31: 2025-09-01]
SubAssemblies/BatteryTray/Docs/Images/Battery Tray SubAssembly Heat Inserts.png

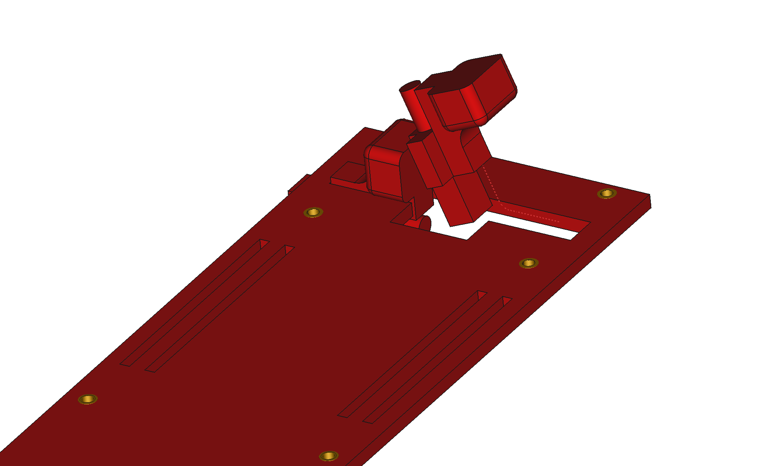
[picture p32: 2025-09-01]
SubAssemblies/BatteryTray/Docs/Images/Thumb Piece Insertion.png

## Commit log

2025-09-01 Adding initial files
    [12vFan.FCStd, 5VBuckConverter.FCStd, 684ZZ_4x9x4_Bearing.FCStd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]
2025-09-01 Updating main image to be assembly
